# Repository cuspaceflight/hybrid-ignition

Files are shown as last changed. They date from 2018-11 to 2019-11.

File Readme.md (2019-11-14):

# Hybrid Rocket Engine Ignition System

This repository contains the design files for the valve controller used by CU Spaceflight to control our hybrid rocket engine. It is capable of actuating up to 10x 24W solenoid valves simultaneously and is controlled over RS422 or USB by a GUI. 

### Repository Layout

* **ChibiOS:** ChibiOS RTOS, developed by Giovanni Di Sirio.
* **agg-kicad:** KiCAD libraries, footprints and scripts developed by Adam Greig.
* **gen-board.h:** Python tool for generating 'board.h' header files for STM32 microcontrollers for use with ChibiOS.
* **m4-gcs:** Python GUI used to control and monitor the valve controller, developed by Greg Brooks.
* **pcb:** Hardware design files including schematic, pcb layout and BOM.
    * **comms:** Communications board project files.
    * **ignition:** Ignition board project files.
    * **lib:** Various schematic symbols.
* **firmware:** Firmware for each of the three sub-systems.
    * **comms-relay:** Full duplex USB to RS422 converter.
    * **comms-router:** Communications interface for the valve controller. Handles receiving packets over RS422 and routing to the firing boards over UART and vice-versa.
    * **ignition:** Actuates valves on command and reports measurements such as currents consumption, output voltage and if the valve coil is plugged in or not.

Developed by Matt Coates (mc955).

### Future Modifications
* The firing LEDs have their cathodes driven to 24v when a channel is armed but not firing. These LEDs should be moved to be driven by the GPIO that drives the gate of the firing FET.
* Flyback diodes are required on the output channels.

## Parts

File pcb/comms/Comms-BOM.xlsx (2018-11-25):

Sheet: Mouser
Order Code | Qty [1] | Qty [3] | Line Note
584-ADP3335ARMZ3.3R | 1 | 3 | 1x ADP3335 MSOP-8

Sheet: RS
Order Code | Qty | Line Note
122-3021 | 1 | 1x--USB Conn--None--X1
125-7930 | 1 | 1x--USB Cap--None--X2
125-7926 | 1 | 1x--RJ45 Cap--None--X4
111-6745 | 1 | 1x--RJ45 Conn--None--X3

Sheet: Farnell
Order Code | Substitute | Qty [3] | Line Note
2122112 | 1469739 | 3 | 1x 0R 0603
2368169 | 2368169 | 21 | 7x ESD_DIODE 0402
9287787 | 9287787 | 2 | 1x Case None
1865556 | 2211167 | 9 | 3x 1u 0603-L
2616742 | 1577593 | 12 | 4x 100R 0603
2496790 | 2496790 | 6 | 2x 10p 0402
2140682 | 2140682 | 3 | 1x 120R 0402
2496814 | 2525024 | 3 | 1x 1u 0402
1753809 | 1753809 | 3 | 1x USB-B USB-B-SKT
1830747 | 1830747 | 3 | 1x 5v In S02B-PASK-2
2362088 | 2672113 | 6 | 2x 2u2 0402
2290328 | 2290328 | 6 | 2x LED 0603-LED
2496771 | 2429353 | 27 | 9x 100n 0402
1462758 | 1462758 | 3 | 1x RJHSE-538x RJHSE-538X
1830748 | 1830748 | 6 | 2x UART1 UART2 S03B-PASK-2
9239111 | 9239111 | 3 | 1x 100 0402
2333377 | 2333377 | 3 | 1x STM32F437VIT6 LQFP-100
2506952 | 2506952 | 3 | 1x 26M XTAL-20x16
2528531 | 2528531 | 3 | 1x MAX14787E SOIC-8
2426952 | 2528756 | 3 | 1x 4u7 0402
2496825 | 2496825 | 3 | 1x 10n 0603-L

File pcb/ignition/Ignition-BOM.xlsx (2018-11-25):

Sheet: Mouser
Order Code | Qty [1] | Qty [3] | Line Note
584-ADP3335ARMZ3.3R | 1 | 3 | 1x ADP3335 MSOP-8
568-SCNAC-MPX | 1 | 1 | AC Input Cover
538-172258-1104 | 10 | 30 | Molex Housings
538-172264-1002 | 20 | 60 | Molex Retainers

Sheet: RS
Order Code | Qty [1] | Qty [3] | Line Note
845-9977 | 1 | 3 | Test Load
771-0448 | 1 | 1 | AC Input Socket
818-3383 | 1 | 1 | AC Input Plug
895-1805 | 80 | 80 | Molex Crimps 20-22 AWG

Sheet: Digikey
Order Code | Qty [1] | Qty [3] | Line Note
LTC4151CMS-1#PBF-ND | 6 | 18 | 6x LTC4151 MSOP-10 IC3 IC4 IC1 IC5 IC2 IC6
1145-1076-ND | 1 | 2 | 1x 24V PSU None X12

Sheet: Farnell
Order Code | Substitute | Qty [3] | Line Note
9238689 | 2303213 | 15 | 5x 47k 0603-L
1435950 | 1435950 | 15 | 5x 0.05R 2512
2447400 | 9238336 | 15 | 5x 56R 0603
2368169 | 2368169 | 12 | 4x ESD_DIODE 0402
1865556 | 2211167 | 6 | 2x 1u 0603-L
2616742 | 1577593 | 27 | 9x 100R 0603
1770616 | 1770616 | 18 | 6x 16A SPST RT33L024
2496790 | 2496790 | 6 | 2x 10p 0402
1107429 | 1107429 | 3 | 1x 0.01R 2512
2494369 | 2494369 | 21 | 7x CH1 CH2 CH3 CH4 CH5 PSU 172
2053833 | 2053833 | 18 | 6x NFET SOT-23
2452032 | 2452032 | 18 | 6x SCHOTTKY SOD-123FL
2723662 | 2723662 | 10 | 5x M12 Socket None
2358234 | 2358234 | 3 | 1x MICROSD MICROSD_MOLEX_50339
2496814 | 2525024 | 3 | 1x 1u 0402
1830747 | 1830747 | 24 | 8x LED1 LED3 LED2 LED5 LED4 5v
2362088 | 2672113 | 6 | 2x 2u2 0402
2138501 | 2138501 | 39 | 13x 110k 0603
2290328 | 2290328 | 6 | 2x LED 0603-LED
2496771 | 2429353 | 27 | 9x 100n 0402
2408407 | 2672214 | 6 | 2x 10u 1206
1830748 | 1830748 | 6 | 2x UART1 UART2 S03B-PASK-2
9239111 | 9239111 | 3 | 1x 100 0402
2332016 | 2332016 | 36 | 12x 10k 0603
1510671 | 1510671 | 15 | 5x D SOD-123F
1581207 | 1581207 | 3 | 1x Bi-LED None
2335726 | 2335726 | 35 | 5x GRN LED None
2333377 | 2333377 | 3 | 1x STM32F437VIT6 LQFP-100
2506952 | 2506952 | 3 | 1x 26M XTAL-20x16
1469740 | 1577605 | 27 | 9x 1k 0603
2426952 | 2528756 | 3 | 1x 4u7 0402
2496825 | 2496825 | 3 | 1x 10n 0603-L
2627737 | 2627737 | 10 | 5x M12 Plug None
2827587 | 2827587 | 1 | 50m Valve Cable
2367724 | 2367724 | 1 | 100m Wire 22 AWG (600VAC, 7A)
9337687 | 9337687 | 15 | 10k Though Hole

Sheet: CPC
Order Code | Qty [1] | Qty [3] | Line Note
SC11628 | 6 | 12 | 6x X3 X5 X7 X11 X15 X23 None
PL00915 | 1 | 1 | Mains Plug 13A Fused

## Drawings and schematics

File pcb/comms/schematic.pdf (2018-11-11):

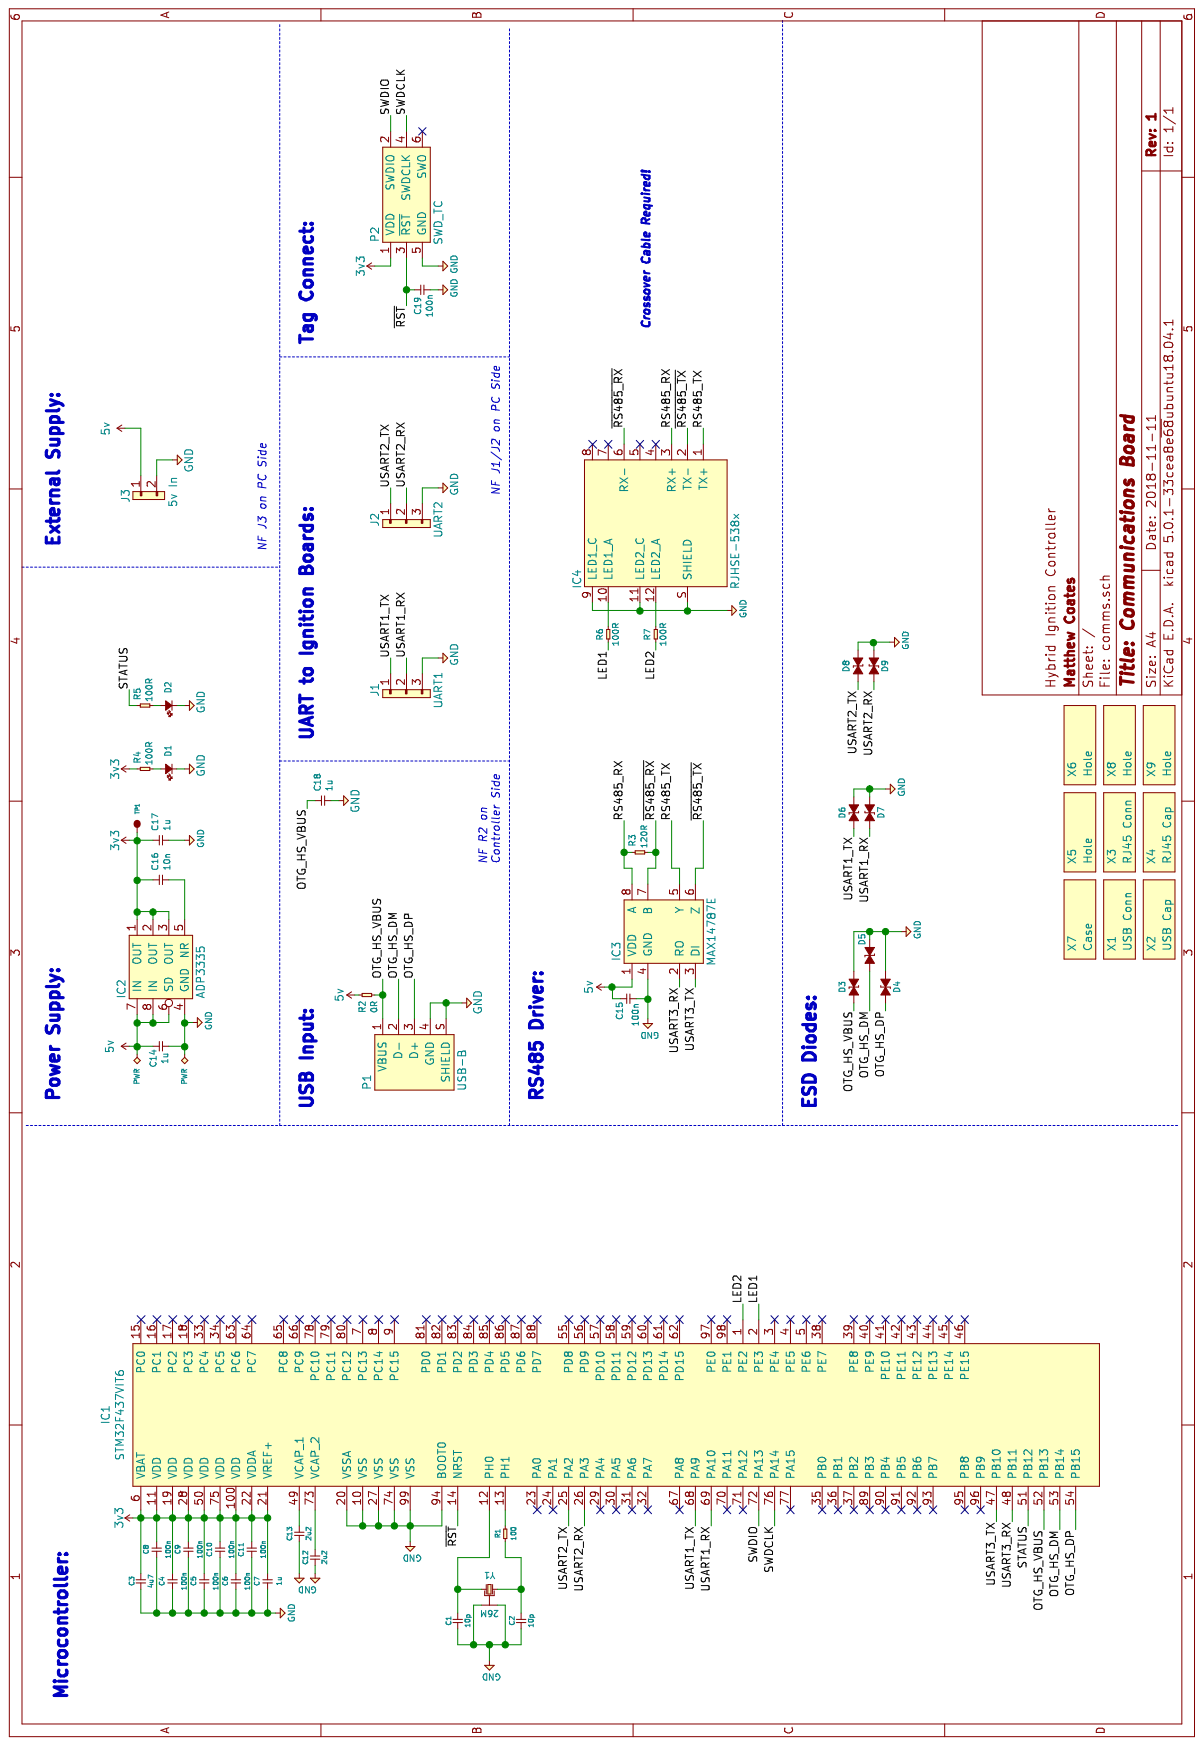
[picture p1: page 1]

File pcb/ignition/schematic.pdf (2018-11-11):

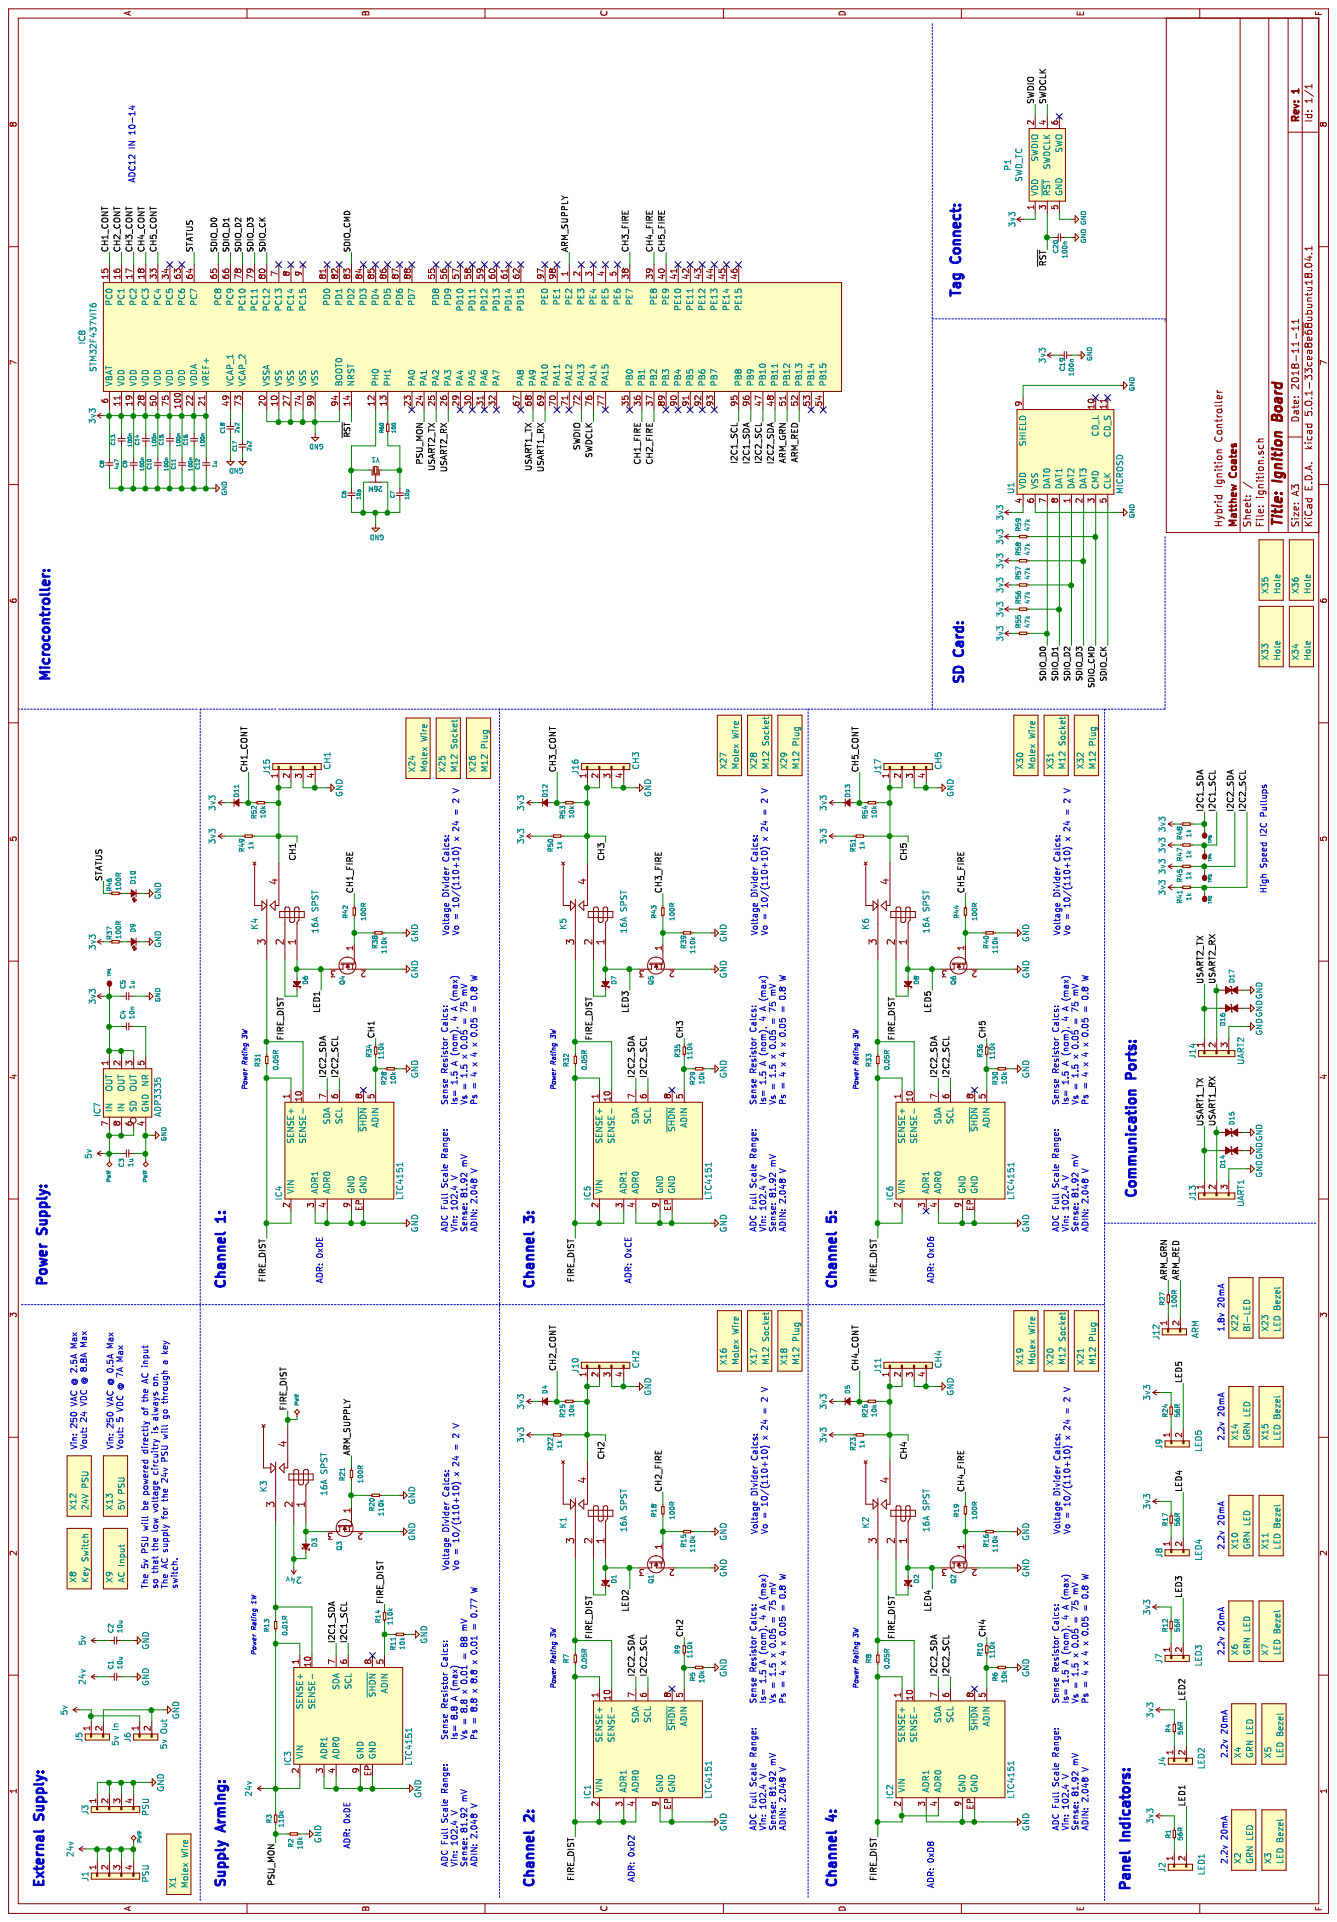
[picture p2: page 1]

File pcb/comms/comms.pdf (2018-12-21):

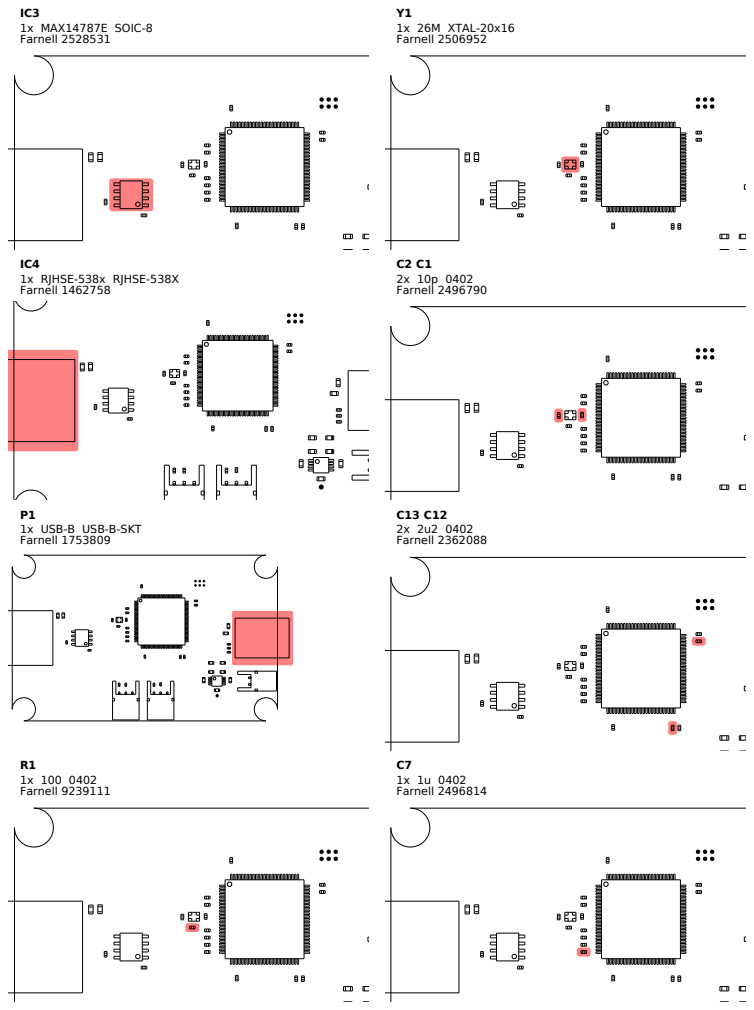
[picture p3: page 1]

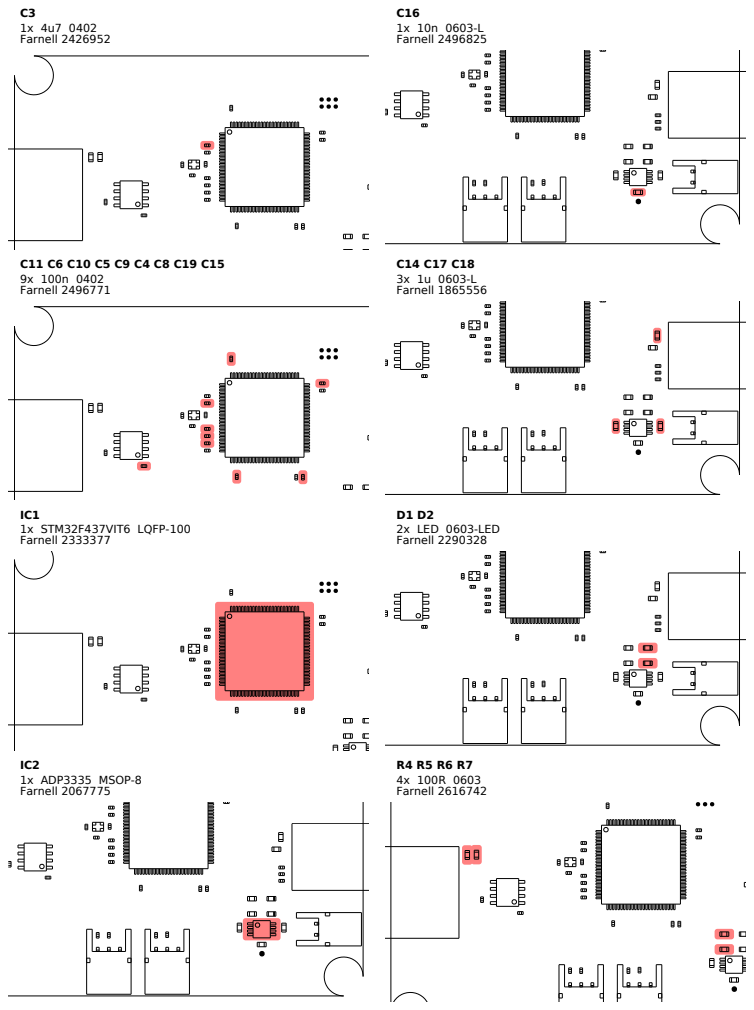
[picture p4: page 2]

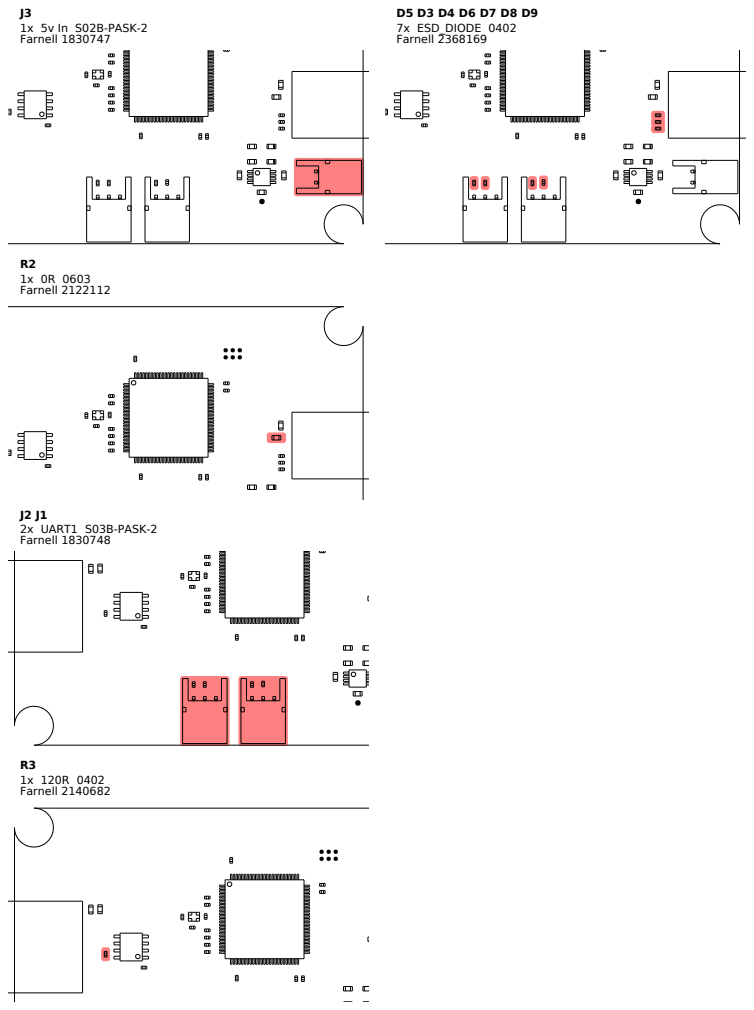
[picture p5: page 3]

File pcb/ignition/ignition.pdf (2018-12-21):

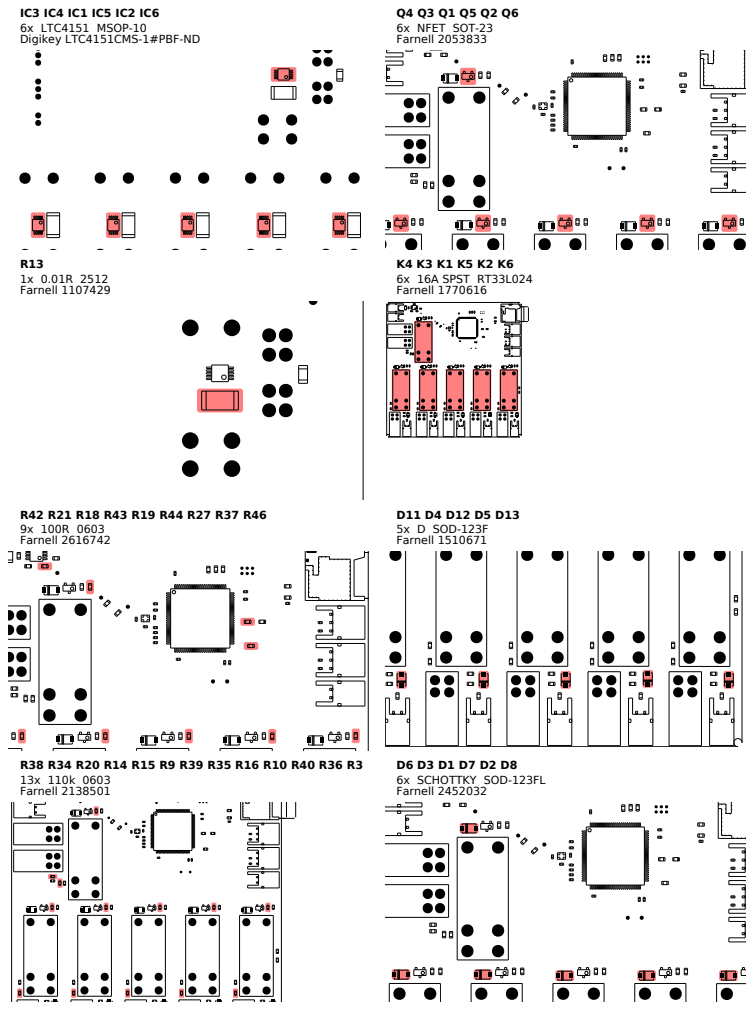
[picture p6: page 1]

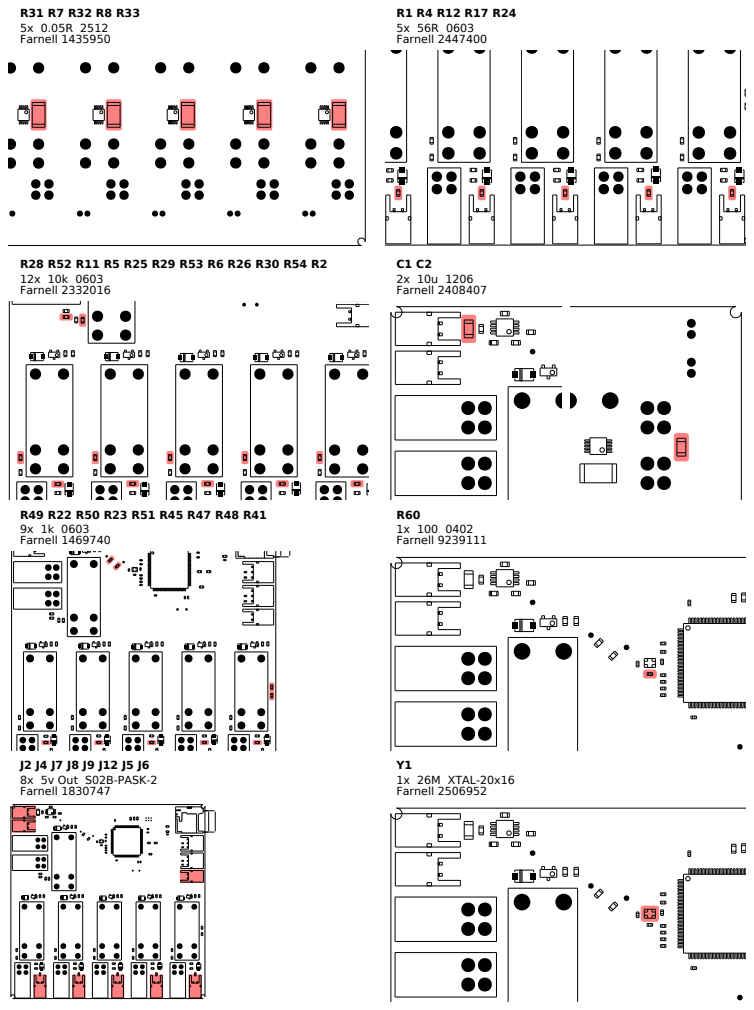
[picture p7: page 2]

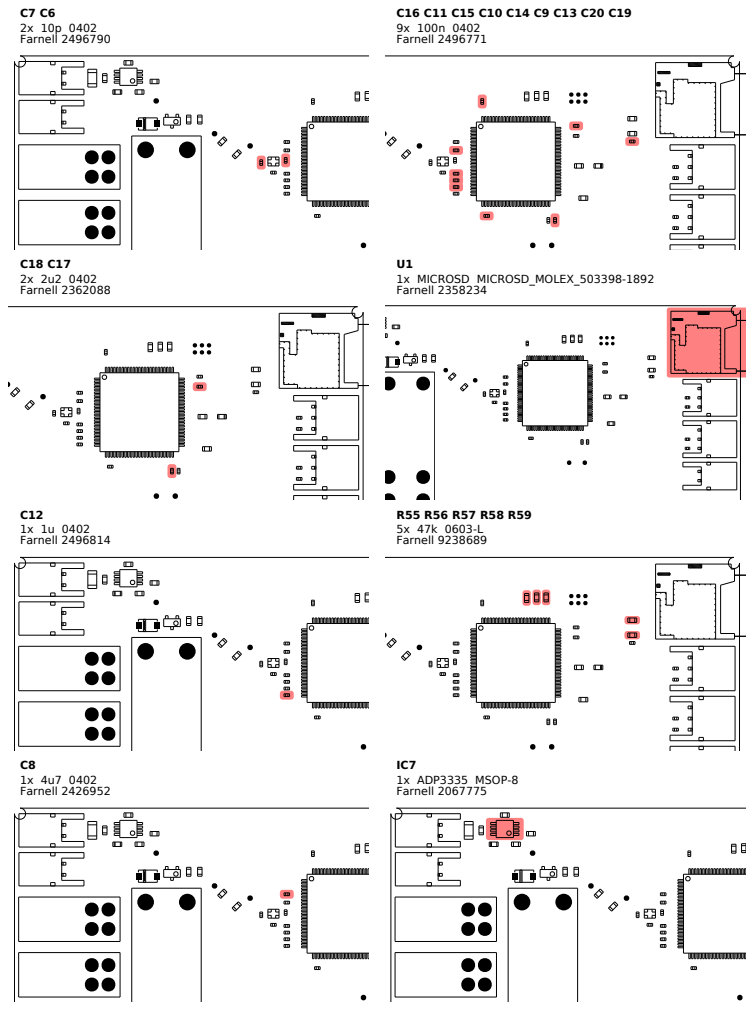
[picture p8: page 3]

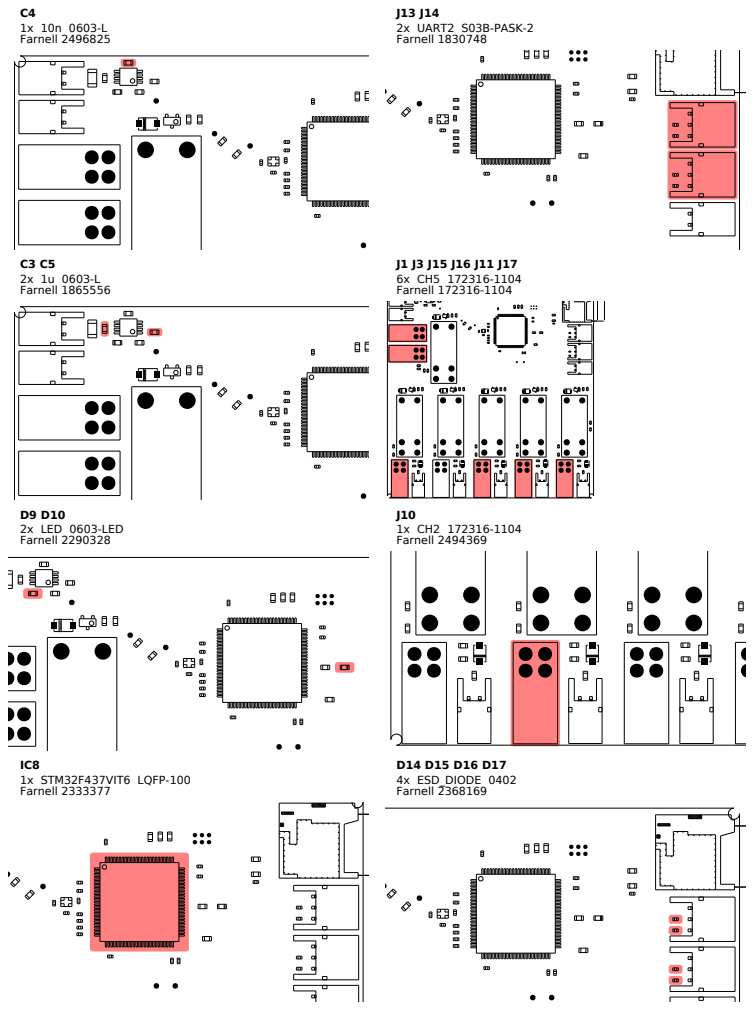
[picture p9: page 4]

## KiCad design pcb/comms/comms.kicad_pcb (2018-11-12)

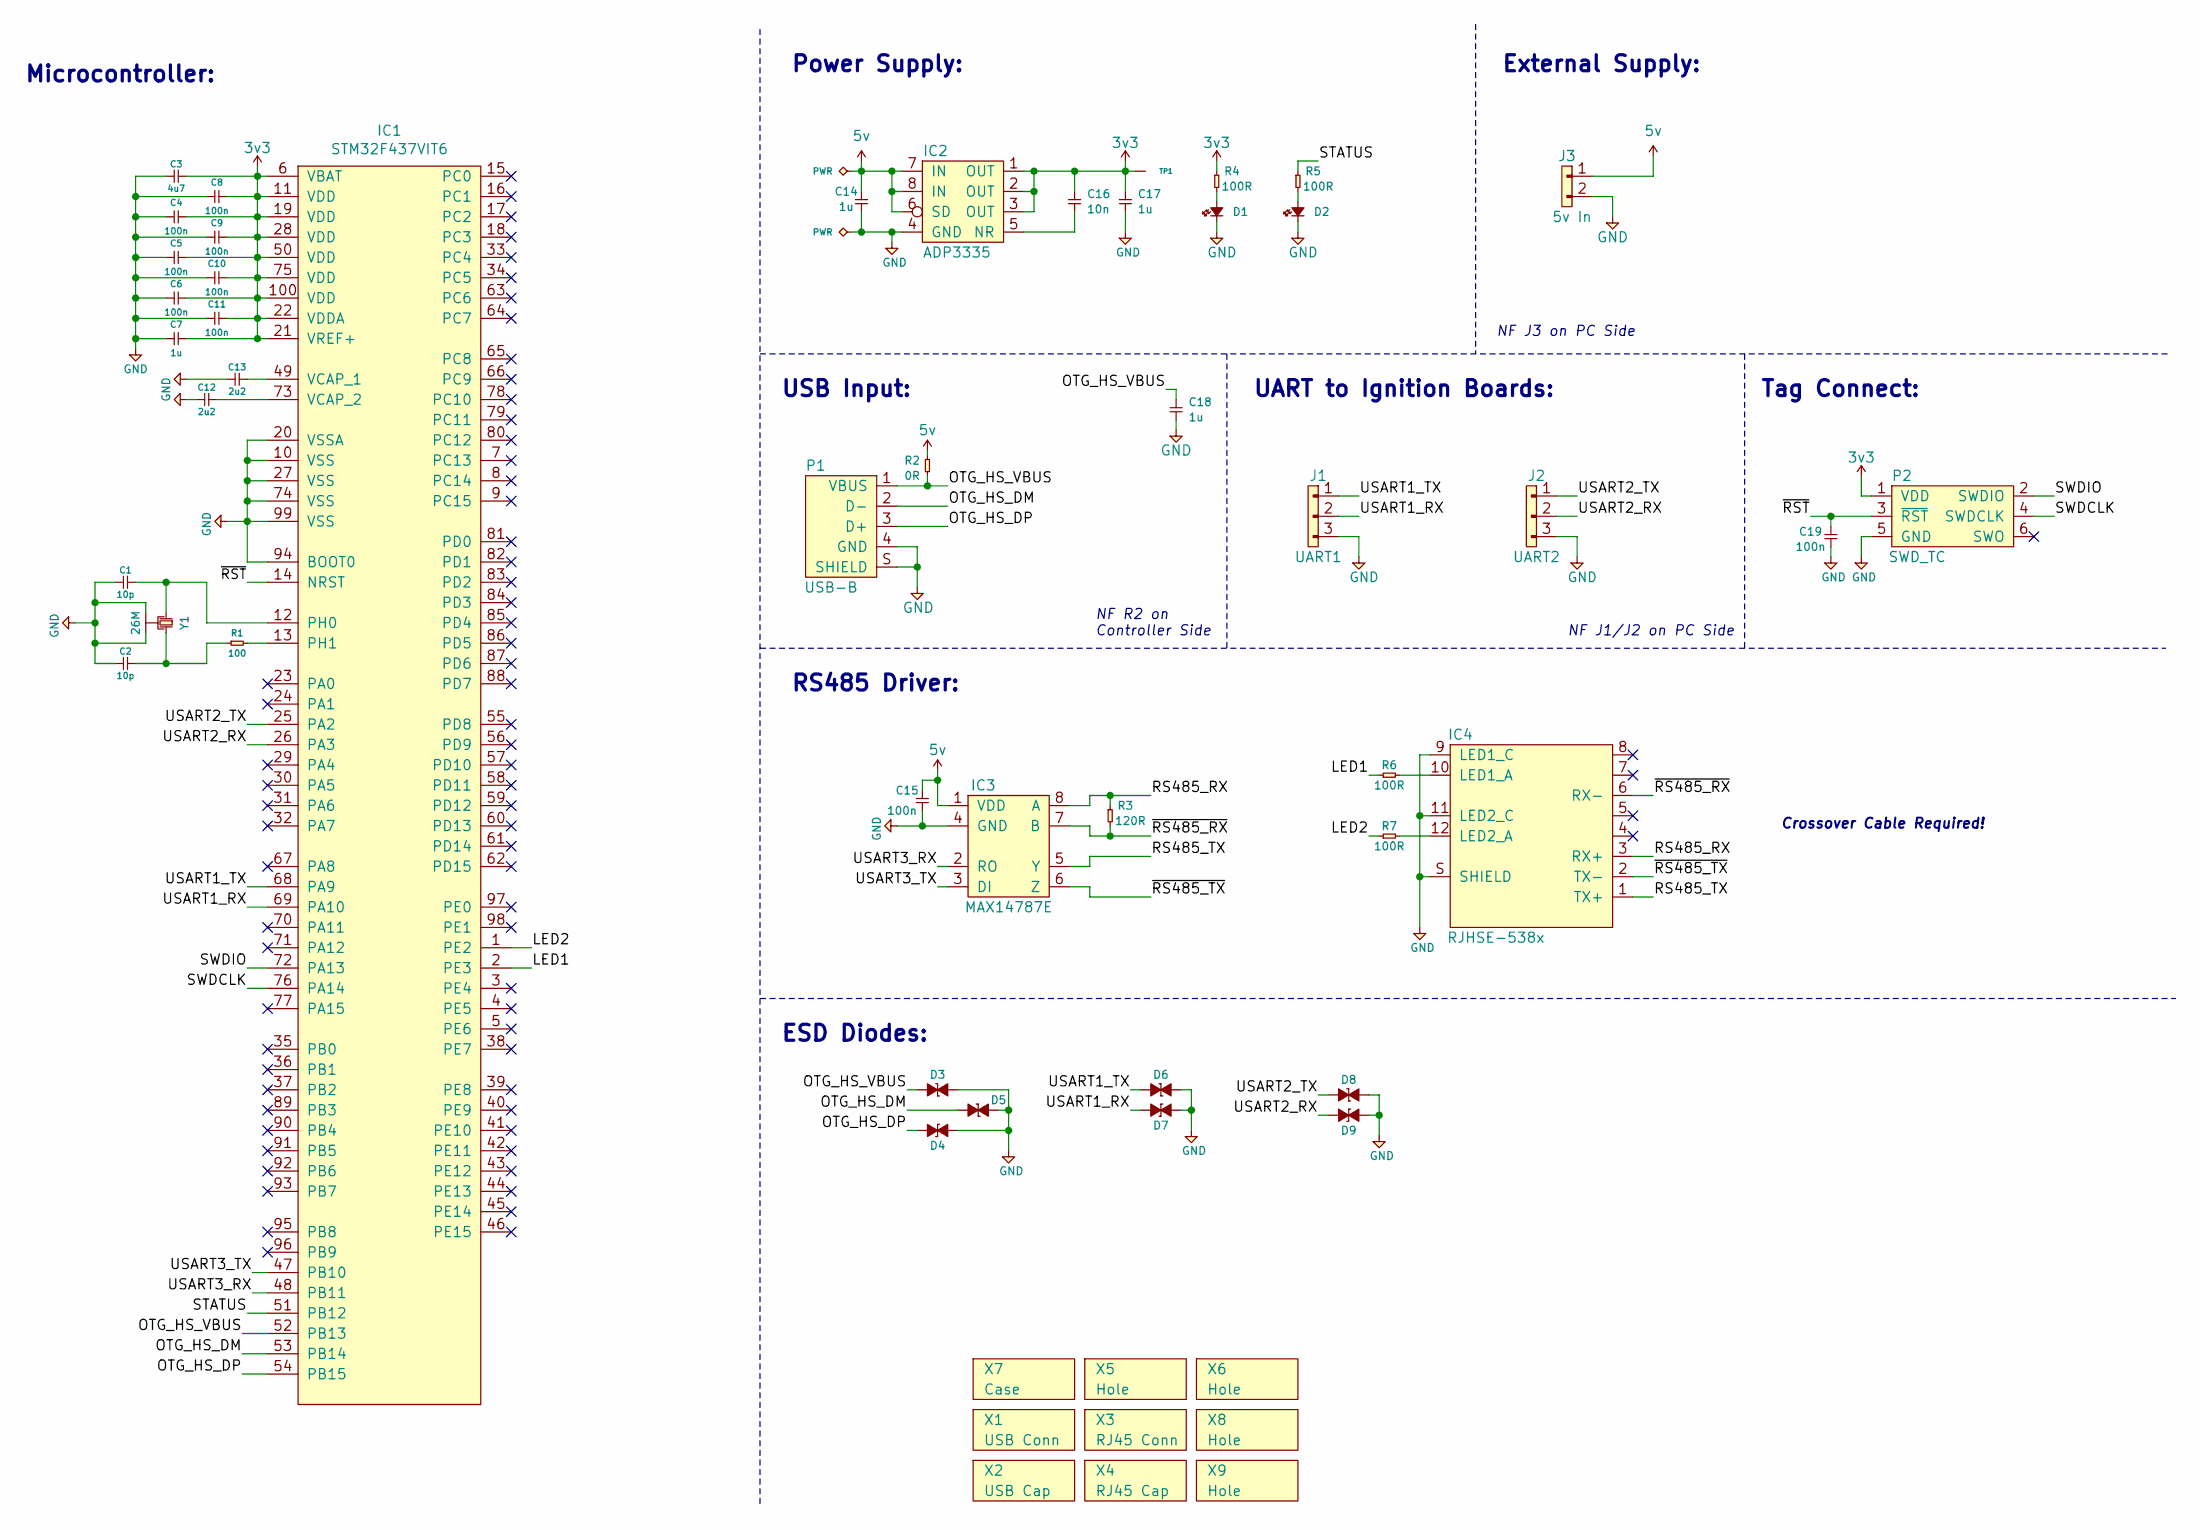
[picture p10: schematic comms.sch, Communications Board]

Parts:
C1, C2: 10p; 0402; Farnell 2496790
C3: 4u7; 0402; Farnell 2426952
C4, C5, C6, C8, C9, C10, C11, C15, C19: 100n; 0402; Farnell 2496771
C7: 1u; 0402; Farnell 2496814
C12, C13: 2u2; 0402; Farnell 2362088
C14, C17, C18: 1u; 0603-L; Farnell 1865556
C16: 10n; 0603-L; Farnell 2496825
D1, D2: LED; 0603-LED; Farnell 2290328
D3, D4, D5, D6, D7, D8, D9: ESD_DIODE; 0402; Farnell 2368169
IC1: STM32F437VIT6; LQFP-100; Farnell 2333377
IC2: ADP3335; MSOP-8; Farnell 2067775
IC3: MAX14787E; SOIC-8; Farnell 2528531
IC4: RJHSE-538x; RJHSE-538X; Farnell 1462758
J1: UART1; S03B-PASK-2; Farnell 1830748
J2: UART2; S03B-PASK-2; Farnell 1830748
J3: 5v In; S02B-PASK-2; Farnell 1830747
P1: USB-B; USB-B-SKT; Farnell 1753809
P2: SWD_TC; TC2030-NL
R1: 100; 0402; Farnell 9239111
R2: 0R; 0603; Farnell 2122112
R3: 120R; 0402; Farnell 2140682
R4, R5, R6, R7: 100R; 0603; Farnell 2616742
TP1: TESTPAD
X1: USB Conn
X2: USB Cap
X3: RJ45 Conn
X4: RJ45 Cap
X5, X6, X8, X9: Hole; M3_MOUNT
X7: Case; Farnell 9287787
Y1: 26M; XTAL-20x16; Farnell 2506952

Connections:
3v3: C3.2, C4.2, C5.2, C6.2, C7.2, C8.2, C9.2, C10.2, C11.2, C16.1, C17.1, IC1.6 (VBAT), IC1.11 (VDD), IC1.19 (VDD), IC1.21 (VREF+), IC1.22 (VDDA), IC1.28 (VDD), IC1.50 (VDD), IC1.75 (VDD), IC1.100 (VDD), IC2.1 (OUT), IC2.2 (OUT), IC2.3 (OUT), P2.1 (VDD), R4.1, TP1.1
5v: C14.1, C15.2, IC2.6 (SD), IC2.7 (IN), IC2.8 (IN), IC3.1 (VDD), J3.1, R2.2
/LED1: IC1.2 (PE3), R6.1
/LED2: IC1.1 (PE2), R7.1
/OTG_HS_DM: D5.1, IC1.53 (PB14), P1.2 (D-)
/OTG_HS_DP: D4.1, IC1.54 (PB15), P1.3 (D+)
/OTG_HS_VBUS: C18.1, D3.1, IC1.52 (PB13), P1.1 (VBUS), R2.1
/RS485_RX: IC3.8 (A), IC4.3 (RX+), R3.1
/RS485_TX: IC3.5 (Y), IC4.1 (TX+)
/STATUS: IC1.51 (PB12), R5.1
/SWDCLK: IC1.76 (PA14), P2.4 (SWDCLK)
/SWDIO: IC1.72 (PA13), P2.2 (SWDIO)
/USART1_RX: D7.1, IC1.69 (PA10), J1.2
/USART1_TX: D6.1, IC1.68 (PA9), J1.1
/USART2_RX: D9.1, IC1.26 (PA3), J2.2
/USART2_TX: D8.1, IC1.25 (PA2), J2.1
/USART3_RX: IC1.48 (PB11), IC3.2 (RO)
/USART3_TX: IC1.47 (PB10), IC3.3 (DI)
/~RS485_RX: IC3.7 (B), IC4.6 (RX-), R3.2
/~RS485_TX: IC3.6 (Z), IC4.2 (TX-)
/~RST: C19.2, IC1.14 (NRST), P2.3 (~RST)
GND: C1.1, C2.1, C3.1, C4.1, C5.1, C6.1, C7.1, C8.1, C9.1, C10.1, C11.1, C12.2, C13.2, C14.2, C15.1, C17.2, C18.2, C19.1, D1.1, D2.1, D3.2, D4.2, D5.2, D6.2, D7.2, D8.2, D9.2, IC1.10 (VSS), IC1.20 (VSSA), IC1.27 (VSS), IC1.74 (VSS), IC1.94 (BOOT0), IC1.99 (VSS), IC2.4 (GND), IC3.4 (GND), IC4.9 (LED1_C), IC4.11 (LED2_C), IC4.S (SHIELD), J1.3, J2.3, J3.2, P1.4 (GND), P1.S (SHIELD), P2.5 (GND), Y1.2, Y1.4
unnamed: C1.2, IC1.12 (PH0), Y1.1
unnamed: C2.2, R1.1, Y1.3
unnamed: C12.1, IC1.73 (VCAP_2)
unnamed: C13.1, IC1.49 (VCAP_1)
unnamed: C16.2, IC2.5 (NR)
unnamed: D1.2, R4.2
unnamed: D2.2, R5.2
unnamed: IC1.13 (PH1), R1.2
unnamed: IC4.10 (LED1_A), R6.2
unnamed: IC4.12 (LED2_A), R7.2

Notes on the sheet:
Microcontroller:
Power Supply:
Tag Connect:
USB Input:
External Supply:
RS485 Driver:
UART to Ignition Boards:
Crossover Cable Required!
NF J1/J2 on PC Side
NF J3 on PC Side
NF R2 on Controller Side
ESD Diodes:

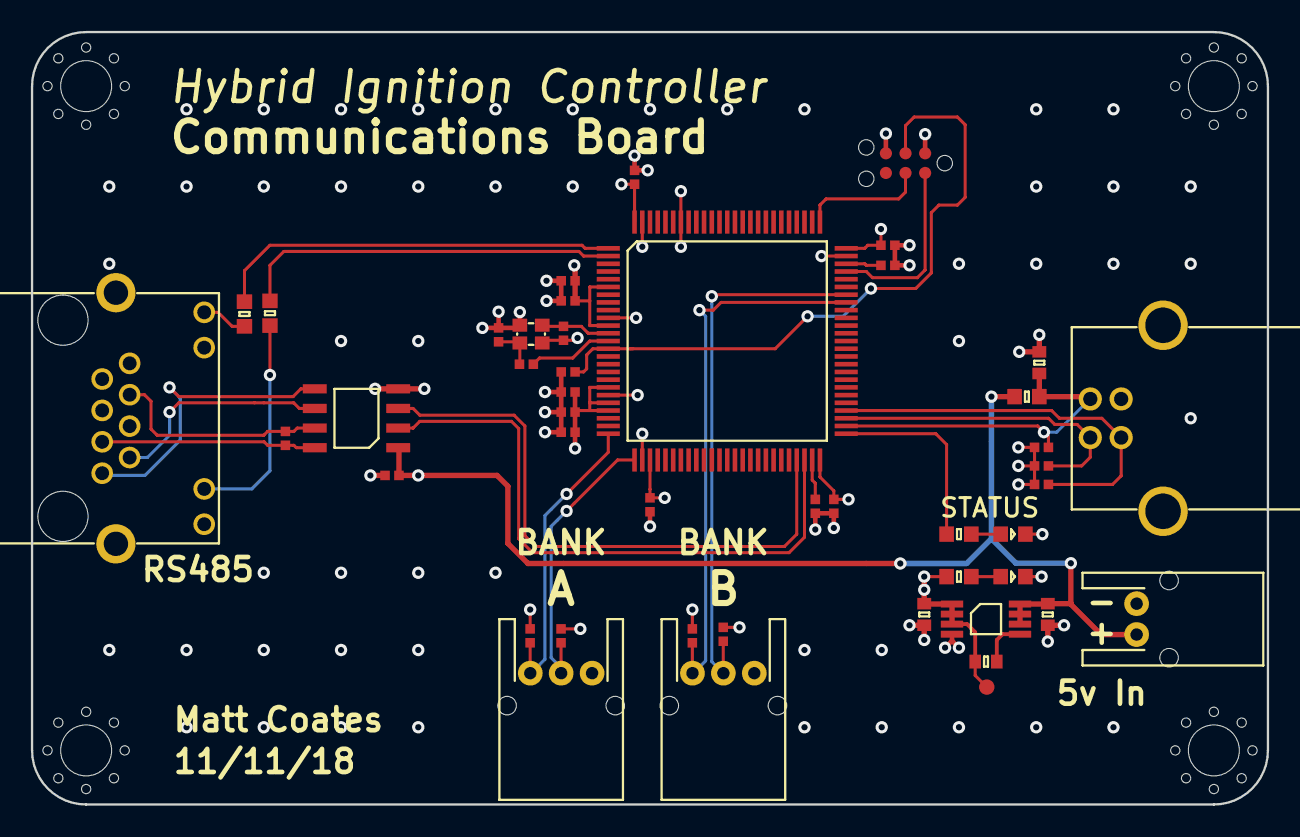
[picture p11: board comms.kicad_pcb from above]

Board: 4 copper layers, 80.0 x 50.0 mm, 50 parts (0 on the bottom side), 32 nets.

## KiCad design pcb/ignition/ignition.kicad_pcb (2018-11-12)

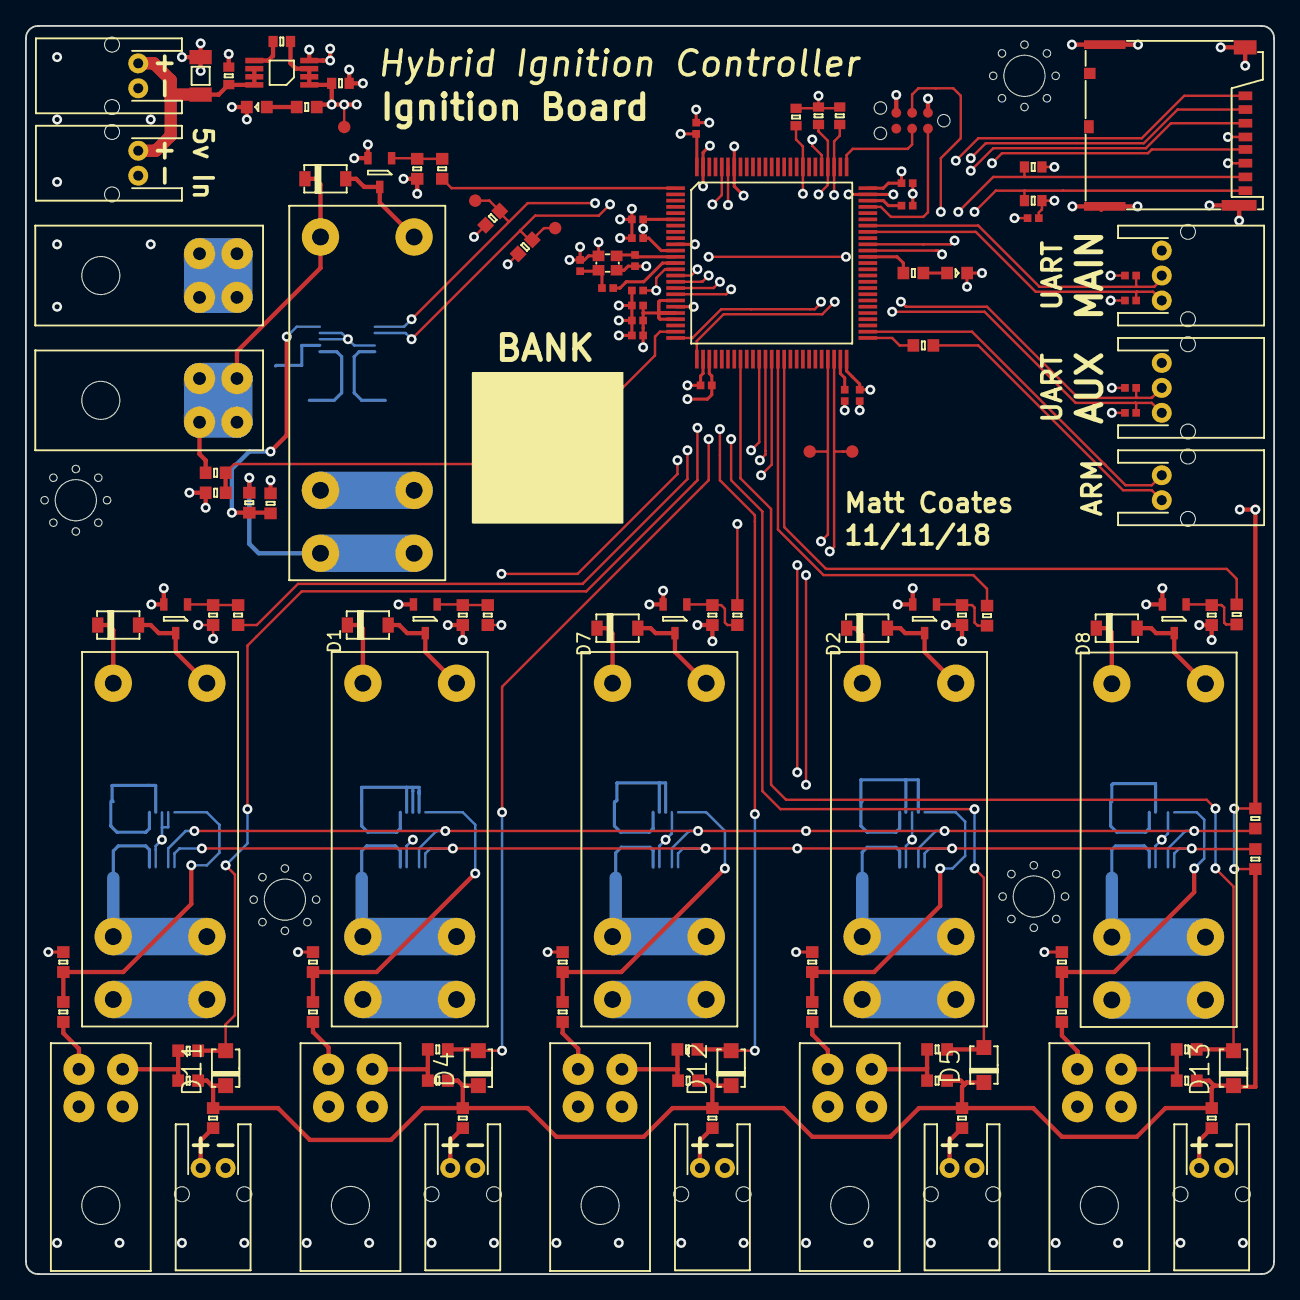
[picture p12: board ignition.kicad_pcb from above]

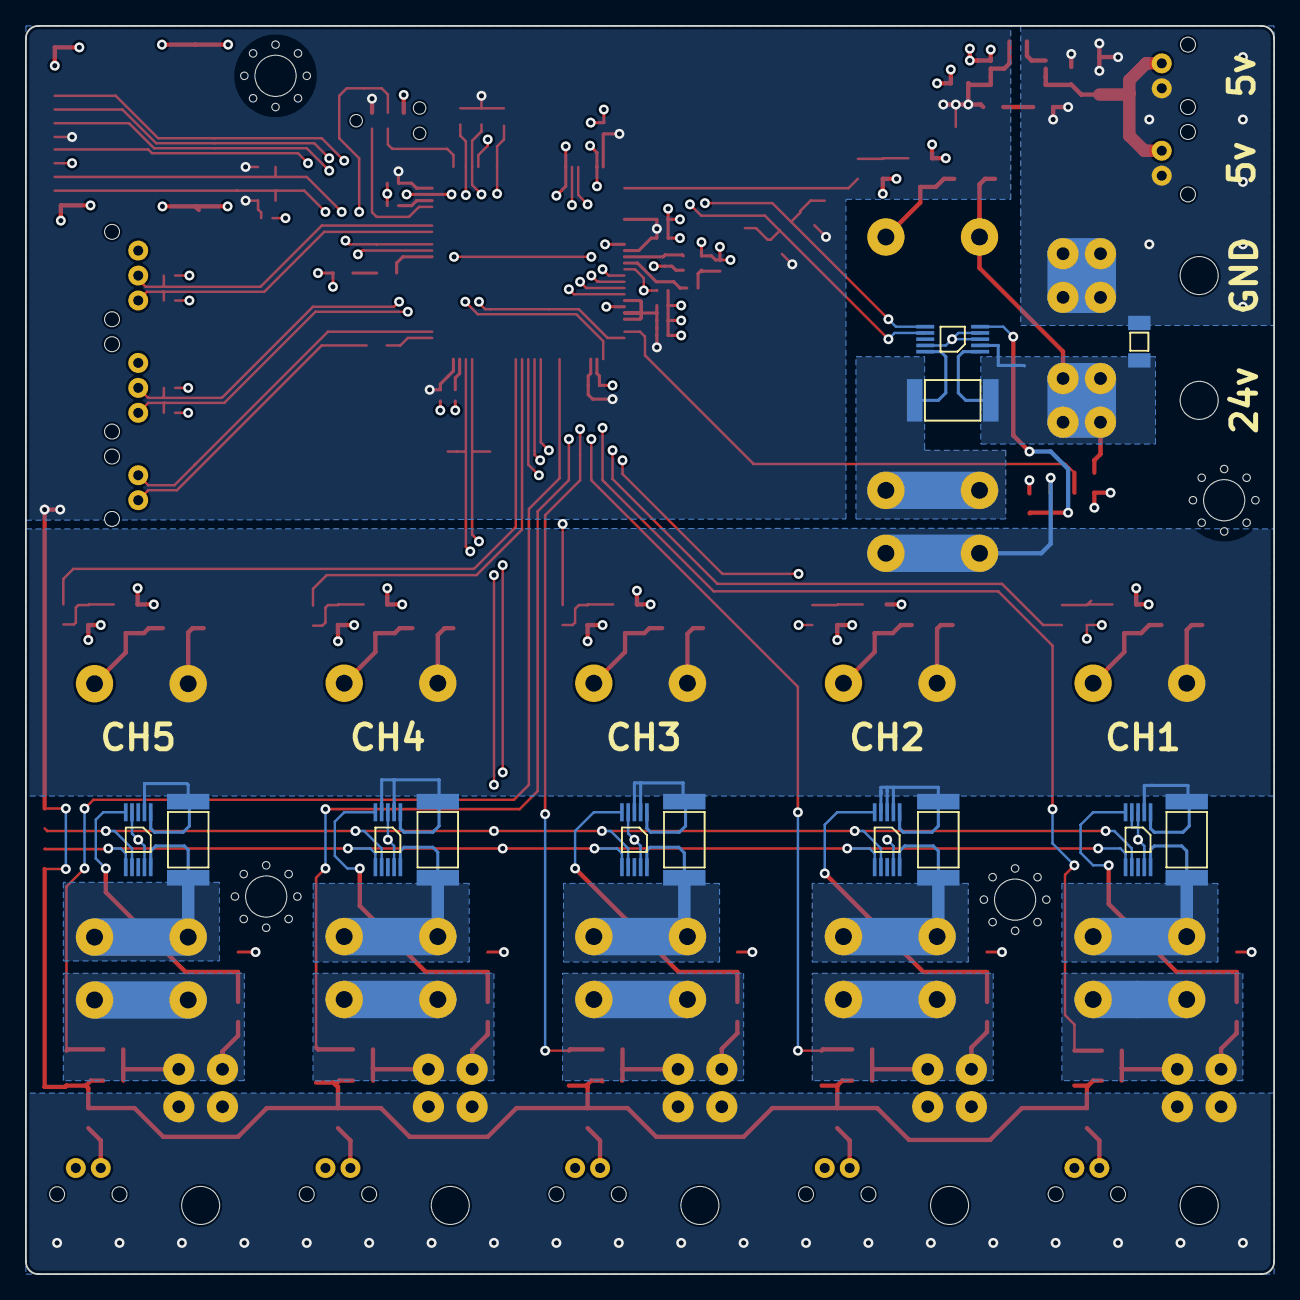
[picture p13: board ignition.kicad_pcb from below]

Board: 4 copper layers, 100.0 x 100.0 mm, 146 parts (13 on the bottom side), 80 nets.

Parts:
C1, C2: 10u; 1206
C3, C5: 1u; 0603-L
C4: 10n; 0603-L
C6, C7: 10p; 0402
C8: 4u7; 0402
C9, C10, C11, C13, C14, C15, C16, C19, C20: 100n; 0402
C12: 1u; 0402
C17, C18: 2u2; 0402
D1, D2, D3, D6, D7, D8: SCHOTTKY; SOD-123FL
D4, D5, D11, D12, D13: D; SOD-123F
D9, D10: LED; 0603-LED
D14, D15, D16, D17: ESD_DIODE; 0402
IC1, IC2, IC3, IC4, IC5, IC6: LTC4151; MSOP-10
IC7: ADP3335; MSOP-8
IC8: STM32F437VIT6; LQFP-100
J1, J3: PSU; 172316-1104
J2: LED1; S02B-PASK-2
J4: LED2; S02B-PASK-2
J5: 5v In; S02B-PASK-2
J6: 5v Out; S02B-PASK-2
J7: LED3; S02B-PASK-2
J8: LED4; S02B-PASK-2
J9: LED5; S02B-PASK-2
J10: CH2; 172316-1104
J11: CH4; 172316-1104
J12: ARM; S02B-PASK-2
J13: UART1; S03B-PASK-2
J14: UART2; S03B-PASK-2
J15: CH1; 172316-1104
J16: CH3; 172316-1104
J17: CH5; 172316-1104
K1, K2, K3, K4, K5, K6: 16A SPST; RT33L024
P1: SWD_TC; TC2030-NL
Q1, Q2, Q3, Q4, Q5, Q6: NFET; SOT-23
R1, R4, R12, R17, R24: 56R; 0603
R2, R5, R6, R11, R25, R26, R28, R29, R30, R52, R53, R54: 10k; 0603
R3, R9, R10, R14, R15, R16, R20, R34, R35, R36, R38, R39, R40: 110k; 0603
R7, R8, R31, R32, R33: 0.05R; 2512
R13: 0.01R; 2512
R18, R19, R21, R27, R37, R42, R43, R44, R46: 100R; 0603
R22, R23, R41, R45, R47, R48, R49, R50, R51: 1k; 0603
R55, R56, R57, R58, R59: 47k; 0603-L
R60: 100; 0402
TP1, TP2, TP3, TP4, TP5: TESTPAD
U1: MICROSD; MICROSD_MOLEX_503398-1892
X33, X34, X35, X36: Hole; M3_MOUNT
Y1: 26M; XTAL-20x16

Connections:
3v3: C4.1, C5.1, C8.2, C9.2, C10.2, C11.2, C12.2, C13.2, C14.2, C15.2, C16.2, C19.1, D4.1, D5.1, D11.1, D12.1, D13.1, IC7.1, IC7.2, IC7.3, IC8.6, IC8.11, IC8.19, IC8.21, IC8.22, IC8.28, IC8.50, IC8.75, IC8.100, P1.1, R1.2, R4.2, R12.2, R17.2, R22.2, R23.2, R24.2, R37.1, R41.2, R45.2, R47.2, R48.2, R49.2, R50.2, R51.2, R55.1, R56.1, R57.1, R58.1, R59.1, TP1.1, U1.4
5v: C2.1, C3.1, IC7.6, IC7.7, IC7.8, J5.1, J6.1
/ARM_GRN: IC8.51, R27.2
/ARM_RED: IC8.52, J12.2
/ARM_SUPPLY: IC8.1, R21.1
/CH1: J15.1, J15.2, K4.4, R34.1, R49.1, R52.1
/CH1_CONT: D11.2, IC8.15, R52.2
/CH1_FIRE: IC8.36, R42.1
/CH2: J10.1, J10.2, K1.4, R9.1, R22.1, R25.1
/CH2_CONT: D4.2, IC8.16, R25.2
/CH2_FIRE: IC8.37, R18.1
/CH3: J16.1, J16.2, K5.4, R35.1, R50.1, R53.1
/CH3_CONT: D12.2, IC8.17, R53.2
/CH3_FIRE: IC8.38, R43.1
/CH4: J11.1, J11.2, K2.4, R10.1, R23.1, R26.1
/CH4_CONT: D5.2, IC8.18, R26.2
/CH4_FIRE: IC8.39, R19.1
/CH5: J17.1, J17.2, K6.4, R36.1, R51.1, R54.1
/CH5_CONT: D13.2, IC8.33, R54.2
/CH5_FIRE: IC8.40, R44.1
/FIRE_DIST: D1.1, D2.1, D6.1, D7.1, D8.1, IC1.1, IC1.2, IC1.3, IC1.4, IC2.1, IC2.2, IC2.4, IC4.1, IC4.2, IC5.1, IC5.2, IC5.3, IC6.1, IC6.2, K1.2, K2.2, K3.4, K4.2, K5.2, K6.2, R7.2, R8.2, R14.1, R31.2, R32.2, R33.2
/I2C1_SCL: IC3.6, IC8.95, R47.1, TP4.1
/I2C1_SDA: IC3.7, IC8.96, R48.1, TP5.1
/I2C2_SCL: IC1.6, IC2.6, IC4.6, IC5.6, IC6.6, IC8.47, R41.1, TP2.1
/I2C2_SDA: IC1.7, IC2.7, IC4.7, IC5.7, IC6.7, IC8.48, R45.1, TP3.1
/LED1: D6.2, J2.2, K4.1, Q4.3
/LED2: D1.2, J4.2, K1.1, Q1.3
/LED3: D7.2, J7.2, K5.1, Q5.3
/LED4: D2.2, J8.2, K2.1, Q2.3
/LED5: D8.2, J9.2, K6.1, Q6.3
/PSU_MON: IC8.24, R2.1, R3.1
/SDIO_CK: IC8.80, U1.5
/SDIO_CMD: IC8.83, R59.2, U1.3
/SDIO_D0: IC8.65, R55.2, U1.7
/SDIO_D1: IC8.66, R56.2, U1.8
/SDIO_D2: IC8.78, R57.2, U1.1
/SDIO_D3: IC8.79, R58.2, U1.2
/STATUS: IC8.64, R46.1
/SWDCLK: IC8.76, P1.4
/SWDIO: IC8.72, P1.2
/USART1_RX: D15.1, IC8.69, J13.2
/USART1_TX: D14.1, IC8.68, J13.1
/USART2_RX: D17.1, IC8.26, J14.2
/USART2_TX: D16.1, IC8.25, J14.1
/~RST: C20.2, IC8.14, P1.3
GND: C1.2, C2.2, C3.2, C5.2, C6.1, C7.1, C8.1, C9.1, C10.1, C11.1, C12.1, C13.1, C14.1, C15.1, C16.1, C17.2, C18.2, C19.2, C20.1, D9.1, D10.1, D14.2, D15.2, D16.2, D17.2, IC1.9, IC2.3, IC2.9, IC3.3, IC3.4, IC3.9, IC4.3, IC4.4, IC4.9, IC5.4, IC5.9, IC6.4, IC6.9, IC7.4, IC8.10, IC8.20, IC8.27, IC8.74, IC8.94, IC8.99, J3.1, J3.2, J3.3, J3.4, J5.2, J6.2, J10.3, J10.4, J11.3, J11.4, J13.3, J14.3, J15.3, J15.4, J16.3, J16.4, J17.3, J17.4, P1.5, Q1.2, Q2.2, Q3.2, Q4.2, Q5.2, Q6.2, R2.2, R5.1, R6.1, R11.1, R15.1, R16.1, R20.1, R28.1, R29.1, R30.1, R38.1, R39.1, R40.1, U1.6, U1.9, Y1.2, Y1.4
unnamed: C4.2, IC7.5
unnamed: C6.2, IC8.12, Y1.1
unnamed: C7.2, R60.1, Y1.3
unnamed: C17.1, IC8.73
unnamed: C18.1, IC8.49
unnamed: D3.2, K3.1, Q3.3
unnamed: D9.2, R37.2
unnamed: D10.2, R46.2
unnamed: IC1.5, R5.2, R9.2
unnamed: IC1.10, K1.3, R7.1
unnamed: IC2.5, R6.2, R10.2
unnamed: IC2.10, K2.3, R8.1
unnamed: IC3.5, R11.2, R14.2
unnamed: IC3.10, K3.3, R13.1
unnamed: IC4.5, R28.2, R34.2
unnamed: IC4.10, K4.3, R31.1
unnamed: IC5.5, R29.2, R35.2
unnamed: IC5.10, K5.3, R32.1
unnamed: IC6.5, R30.2, R36.2
unnamed: IC6.10, K6.3, R33.1
unnamed: IC8.13, R60.2
unnamed: J2.1, R1.1
unnamed: J4.1, R4.1
unnamed: J7.1, R12.1
unnamed: J8.1, R17.1
unnamed: J9.1, R24.1
unnamed: J12.1, R27.1
unnamed: Q1.1, R15.2, R18.2
unnamed: Q2.1, R16.2, R19.2
unnamed: Q3.1, R20.2, R21.2
unnamed: Q4.1, R38.2, R42.2
unnamed: Q5.1, R39.2, R43.2
unnamed: Q6.1, R40.2, R44.2
VCC: C1.1, D3.1, IC3.1, IC3.2, J1.1, J1.2, J1.3, J1.4, K3.2, R3.2, R13.2

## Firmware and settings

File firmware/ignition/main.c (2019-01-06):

#include "ch.h"
#include "hal.h"

#include "uart.h"
#include "state.h"
#include "analog.h"
#include "ltc4151.h"

int main(void) {

    /* Allow debug access during WFI sleep */
    DBGMCU->CR |= DBGMCU_CR_DBG_SLEEP;

    /* Initialise ChibiOS */
    halInit();
    chSysInit();

    /* Initialise UART */
    uart_init(&SD1);

    /* Initialise ADC */
    analog_init();

    /* Initialise LTC4151 Bus */
    ltc4151_init_bus();

    /* Initialise State Machine */
    state_init();

    /* Status LED */
    while(true){
        palToggleLine(LINE_STATUS);
        chThdSleepMilliseconds(500);
    }

    /* Do Nothing */
    chThdSleep(TIME_INFINITE);
}

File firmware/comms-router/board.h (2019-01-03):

/*
    ChibiOS - Copyright (C) 2006..2016 Giovanni Di Sirio
    Licensed under the Apache License, Version 2.0 (the "License");
    you may not use this file except in compliance with the License.
    You may obtain a copy of the License at
    http://www.apache.org/licenses/LICENSE-2.0
    Unless required by applicable law or agreed to in writing, software
    distributed under the License is distributed on an "AS IS" BASIS,
    WITHOUT WARRANTIES OR CONDITIONS OF ANY KIND, either express or implied.
    See the License for the specific language governing permissions and
    limitations under the License.
*/

/*
    Generated by gen-board.h.py based on ./board.yaml
*/

#ifndef _BOARD_H_
#define _BOARD_H_


/*
    Setup for comms_router
*/

/*
    Board identifier
*/
#define BOARD_COMMS_ROUTER
#define BOARD_NAME                     "comms_router"

/*
    Board oscillators-related settings.
*/
#if !defined(STM32_LSECLK)
#define STM32_LSECLK                   0U
#endif

#if !defined(STM32_HSECLK)
#define STM32_HSECLK                   26000000U
#endif

/*
    Board voltages
    Required for performance limits calculation.
*/
#define STM32_VDD                      330U

/*
    MCU type as defined in the ST header.
*/
#define STM32F437xx


/*
    IO pins assignments.
*/
#define GPIOA_PIN0                     0U
#define GPIOA_PIN1                     1U
#define GPIOA_BANK_A_TX                2U
#define GPIOA_BANK_A_RX                3U
#define GPIOA_PIN4                     4U
#define GPIOA_PIN5                     5U
#define GPIOA_PIN6                     6U
#define GPIOA_PIN7                     7U
#define GPIOA_PIN8                     8U
#define GPIOA_BANK_B_TX                9U
#define GPIOA_BANK_B_RX                10U
#define GPIOA_PIN11                    11U
#define GPIOA_PIN12                    12U
#define GPIOA_SWDIO                    13U
#define GPIOA_SWCLK                    14U
#define GPIOA_PIN15                    15U

#define GPIOB_PIN0                     0U
#define GPIOB_PIN1                     1U
#define GPIOB_PIN2                     2U
#define GPIOB_PIN3                     3U
#define GPIOB_PIN4                     4U
#define GPIOB_PIN5                     5U
#define GPIOB_PIN6                     6U
#define GPIOB_PIN7                     7U
#define GPIOB_PIN8                     8U
#define GPIOB_PIN9                     9U
#define GPIOB_RS485_TX                 10U
#define GPIOB_RS485_RX                 11U
#define GPIOB_STATUS                   12U
#define GPIOB_OTG_VBUS                 13U
#define GPIOB_OTG_HS_DM                14U
#define GPIOB_OTG_HS_DP                15U

#define GPIOC_PIN0                     0U
#define GPIOC_PIN1                     1U
#define GPIOC_PIN2                     2U
#define GPIOC_PIN3                     3U
#define GPIOC_PIN4                     4U
#define GPIOC_PIN5                     5U
#define GPIOC_PIN6                     6U
#define GPIOC_PIN7                     7U
#define GPIOC_PIN8                     8U
#define GPIOC_PIN9                     9U
#define GPIOC_PIN10                    10U
#define GPIOC_PIN11                    11U
#define GPIOC_PIN12                    12U
#define GPIOC_PIN13                    13U
#define GPIOC_PIN14                    14U
#define GPIOC_PIN15                    15U

#define GPIOD_PIN0                     0U
#define GPIOD_PIN1                     1U
#define GPIOD_PIN2                     2U
#define GPIOD_PIN3                     3U
#define GPIOD_PIN4                     4U
#define GPIOD_PIN5                     5U
#define GPIOD_PIN6                     6U
#define GPIOD_PIN7                     7U
#define GPIOD_PIN8                     8U
#define GPIOD_PIN9                     9U
#define GPIOD_PIN10                    10U
#define GPIOD_PIN11                    11U
#define GPIOD_PIN12                    12U
#define GPIOD_PIN13                    13U
#define GPIOD_PIN14                    14U
#define GPIOD_PIN15                    15U

#define GPIOE_PIN0                     0U
#define GPIOE_PIN1                     1U
#define GPIOE_LED2                     2U
#define GPIOE_LED1                     3U
#define GPIOE_PIN4                     4U
#define GPIOE_PIN5                     5U
#define GPIOE_PIN6                     6U
#define GPIOE_PIN7                     7U
#define GPIOE_PIN8                     8U
#define GPIOE_PIN9                     9U
#define GPIOE_PIN10                    10U
#define GPIOE_PIN11                    11U
#define GPIOE_PIN12                    12U
#define GPIOE_PIN13                    13U
#define GPIOE_PIN14                    14U
#define GPIOE_PIN15                    15U
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

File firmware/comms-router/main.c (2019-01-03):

#include "ch.h"
#include "hal.h"

#include "rs422.h"
#include "uart_a.h"
#include "uart_b.h"
#include "router.h"
#include "usbserial.h"


int main(void) {

    /* Allow debug access during WFI sleep */
    DBGMCU->CR |= DBGMCU_CR_DBG_SLEEP;

    /* Initialise ChibiOS */
    halInit();
    chSysInit();

    /* Initialise USB Serial */
    usbserial_init();

    /* Initialise RS422 */
    rs422_init(&SD3);

    /* Initialise Bank A UART */
    bank_a_uart_init(&SD2);

    /* Initialise Bank B UART */
    bank_b_uart_init(&SD1);

    /* Initialise Packet Router */
    router_init();

    /* Ready LED */
    palSetLine(LINE_LED1);

    /* Status LED */
    while(true){
        palToggleLine(LINE_STATUS);
        chThdSleepMilliseconds(500);
    }

    /* Do Nothing */
    chThdSleep(TIME_INFINITE);
}

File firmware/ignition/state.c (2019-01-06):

#include "ch.h"
#include "hal.h"

#include <string.h>

#include "uart.h"
#include "state.h"
#include "analog.h"
#include "valves.h"
#include "packets.h"
#include "ltc4151.h"
#include "checksum.h"

#define PSU_LDO_THRESH  20000

/* Global Variables */
static uint8_t bank_id = 0;
analog analog_readings;
valve_state valves;
LTC4151 ltc_supply, ltc_ch[5];

/* Uplink Parameters */
systime_t last_packet = 0;
const int upload_int_ms = 200;

/* State Machine Definitions */
typedef enum {
    STATE_INIT=0, STATE_ISOLATED, STATE_SAFE, STATE_ARMED, NUM_STATES
} state_t;

typedef state_t state_func_t(void);

/* State Functions */
state_t run_state(state_t cur_state);
static state_t do_state_init(void);
static state_t do_state_isolated(void);
static state_t do_state_safe(void);
static state_t do_state_armed(void);

/* State Table */
state_func_t* const state_table[NUM_STATES] = {
    do_state_init, do_state_isolated, do_state_safe, do_state_armed
};

/* State Table Lookup */
state_t run_state(state_t cur_state){
    return state_table[cur_state]();
};



/* STATE 1 - Initialisation */
static state_t do_state_init(void){
    
    /* Clear Arming LED */
    palClearLine(LINE_ARM_GRN);
    palClearLine(LINE_ARM_RED);

    /* Turn Off all Valves */
    for(int i=0; i<5; i++){
        valves.ch_state[i] = VALVE_STATE_OFF;
    }
    set_valves(&valves);

    /* De-Energize Firing Bus */
    palClearLine(LINE_ARM_SUPPLY);

    /* Initialise LTC4151 Devices */
    ltc4151_init(&ltc_supply, &I2CD1, LTC4151_ADDR_SUPPLY, 0.01f);
    ltc4151_init(&ltc_ch[0], &I2CD2, LTC4151_ADDR_CH1, 0.05f);
    ltc4151_init(&ltc_ch[1], &I2CD2, LTC4151_ADDR_CH2, 0.05f);
    ltc4151_init(&ltc_ch[2], &I2CD2, LTC4151_ADDR_CH3, 0.05f);
    ltc4151_init(&ltc_ch[3], &I2CD2, LTC4151_ADDR_CH4, 0.05f);
    ltc4151_init(&ltc_ch[4], &I2CD2, LTC4151_ADDR_CH5, 0.05f);

    /* Find Myself */
    packet config_packet;
    while(bank_id == 0){
        if(get_packet(&config_packet)){
            if((config_packet.packet_type == PACKET_CONFIG) && (is_valid(&config_packet))){
                bank_id = config_packet.payload[0];
            }
        }
    }

    return STATE_ISOLATED;
}



/* STATE 2 - Isolated (e.g. Key Switch in SAFE Position) */
static state_t do_state_isolated(void){
    
    /* NO 24V SUPPLY IN THIS STATE */

    /* Clear Arming LED */
    palClearLine(LINE_ARM_GRN);
    palClearLine(LINE_ARM_RED);

    /* Turn Off all Valves */
    for(int i=0; i<5; i++){
        valves.ch_state[i] = VALVE_STATE_OFF;
    }
    set_valves(&valves);

    /* De-Energize Firing Bus */
    palClearLine(LINE_ARM_SUPPLY);

    /* Flush Any Packets */
    packet tmp;
    get_packet(&tmp);

    /* Take Analog Measurements */
    get_analog_values(&analog_readings);

    /* Upload Bank & Channel Status */
    if((chVTGetSystemTime() - last_packet) > MS2ST(upload_int_ms)){

        /* BANK STATUS PACKET */
        packet bank_status_pkt;
        payload_bank_status bank_data;

        /* Populate Payload Data */
        bank_data.bank = bank_id;
        bank_data.state = BANK_STATE_ISOLATED;
        bank_data.mcu_temp = analog_readings.mcu_temp;
        bank_data.psu_voltage = analog_readings.psu_voltage;
        bank_data.firing_bus_voltage = 0;
        bank_data.firing_bus_current = 0;

        /* Populate Bank Status Packet */
        memset(&bank_status_pkt, 0, sizeof(packet));
        bank_status_pkt.packet_type = PACKET_BANK_STATUS;
        bank_status_pkt.timestamp = chVTGetSystemTime();
        memcpy(bank_status_pkt.payload, &bank_data, sizeof(payload_bank_status));
        bank_status_pkt.checksum = fletcher_32(&bank_status_pkt);

        /* Send Bank Status Packet */
        send_packet(&bank_status_pkt);


        /* CHANNEL STATUS PACKET */
        packet channel_status_pkt;
        payload_channel_status channel_data;

        /* Populate Payload Data */
        channel_data.bank = bank_id;
        for(int j=0; j<5; j++){
            channel_data.ch_data[j].state = valves.ch_state[j];
            channel_data.ch_data[j].firing_bus_voltage = 0;
            channel_data.ch_data[j].output_voltage = 0;
            channel_data.ch_data[j].output_current = 0;
            channel_data.ch_data[j].continuity = analog_readings.ch_cont[j];
        }

        /* Populate Channel Status Packet */
        memset(&channel_status_pkt, 0, sizeof(packet));
        channel_status_pkt.packet_type = PACKET_CHANNEL_STATUS;
        channel_status_pkt.timestamp = chVTGetSystemTime();
        memcpy(channel_status_pkt.payload, &channel_data, sizeof(payload_channel_status));
        channel_status_pkt.checksum = fletcher_32(&channel_status_pkt);

        /* Send Channel Status Packet */
        send_packet(&channel_status_pkt);

        /* Time of Last Packet TX */
        last_packet = chVTGetSystemTime();
    }


    /* Detect Ket Switch and Switch State */
    if(analog_readings.psu_voltage > PSU_LDO_THRESH){
        return STATE_SAFE;
    } else {
        return STATE_ISOLATED;
    }
}
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

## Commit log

2018-10-22 started project
    [ignition.kicad_pcb, ignition.sch]
2018-10-24 arming circuit done, started ch1 but need to add continuity
    [ignition.kicad_pcb, ignition.sch]
2018-10-29 added valve channels
    [ignition.kicad_pcb, ignition.sch]
2018-11-02 made progress
    [ignition.sch]
2018-11-03 finished schematic
    [ignition.kicad_pcb, ignition.sch]
2018-11-03 changed key switch
    [ignition.sch]
2018-11-03 finalised schematic, started pcb component placement
    [ignition.kicad_pcb, ignition.sch]
2018-11-06 ignition pcb almost complete
    [ignition.kicad_pcb, ignition.sch]
2018-11-07 pcb routing finished
    [ignition.kicad_pcb]
2018-11-09 finished comms schematic
    [comms.kicad_pcb, comms.sch]
2018-11-11 finished comms board
    [comms.kicad_pcb, comms.sch]
2018-11-11 finalised schematic and pcb copper, adding silk
    [ignition.kicad_pcb, ignition.sch]
2018-11-11 pcbs complete
    [comms.kicad_pcb, ignition.kicad_pcb]
2018-11-11 made changes to ignition as per review
    [ignition-B.Cu.gbr, ignition-B.Mask.gbr, ignition-B.SilkS.gbr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]
2018-11-11 made changes to comms as per review
    [comms-B.Cu.gbr, comms-B.Mask.gbr, comms-B.SilkS.gbr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]
2018-11-12 generated gerbers for comms
    [comms-B.Cu.gbr, comms-B.Mask.gbr, comms-B.SilkS.gbr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]
2018-11-12 generated gerbers for ignition
    [ignition-B.Cu.gbr, ignition-B.Mask.gbr, ignition-B.SilkS.gbr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]
2018-11-12 production ready gerbers for ignition
    [ignition-B.Cu.gbl, ignition-B.Mask.gbr, ignition-B.Mask.gbs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]
2018-11-12 production ready gerbers
    [comms-B.Cu.gbl, comms-B.Mask.gbr, comms-B.Mask.gbs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]
2018-11-25 added Boms
    [Comms-BOM.xlsx, Ignition-BOM.xlsx, ignition.sch]
2018-12-21 generated final sticker bom
2018-12-21 comms-relay firmware template
2018-12-27 changed comment in rs422.c and added ignition board.yaml
2018-12-28 testing i2c
2018-12-29 tested working analog driver
2018-12-31 working ltc4151 driver
2019-01-02 successful test of ADC and LTC4151s
2019-01-03 packet routing comms board almost finished
2019-01-03 comms relay and router finished and tested
2019-01-06 state machine progress, arm command works
2019-01-06 safe state working, now just to finish arm
